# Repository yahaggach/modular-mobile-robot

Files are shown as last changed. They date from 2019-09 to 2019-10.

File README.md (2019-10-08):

# Modular Slam Robot

## Project summary

This project focuses on localization based experiments (e.g echolocation SLAM) and aims at providing a mobile modular robot. The robot and acts as a basis for various experiments with a shared mobile aspect. The modularity of the robot comes in two variants :  

  - Hardware : specific experimentation hardware can be mounted on top of the robot.
  - Software : the raspberry pi as well as power electronics ensure interoperability with most hardware.  

<p align="center">
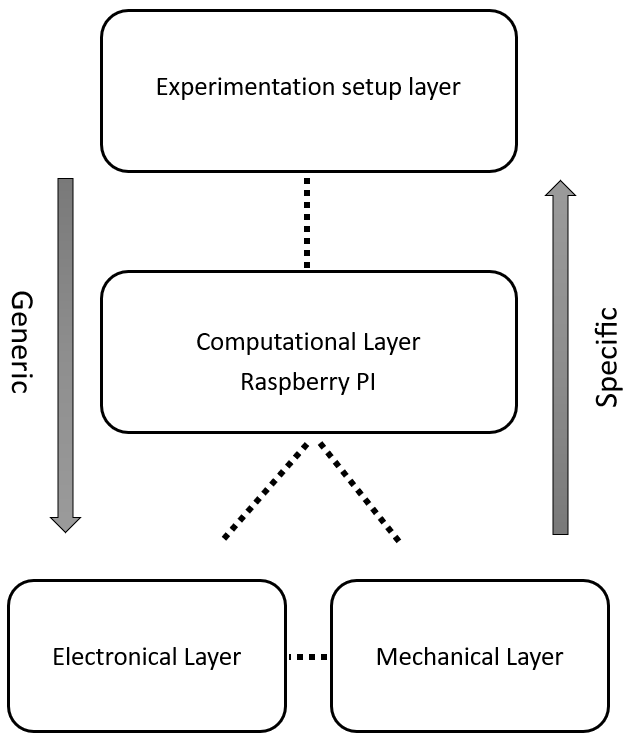
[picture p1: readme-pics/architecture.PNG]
Robot General Architecture
  
</p>  

The robot was developped at LCAV (Audiovisual Communications Laboratory) of EPFL (École Polytechnique Fédérale de Lausanne) under supervision of : Dümbgen Frederike, Krekovic Miranda and Pacholska Michalina. The robot was tested on two separate experiments : EchoSLAM and Indoor Wifi localization.  

## Robot technical summary

<p align="center">
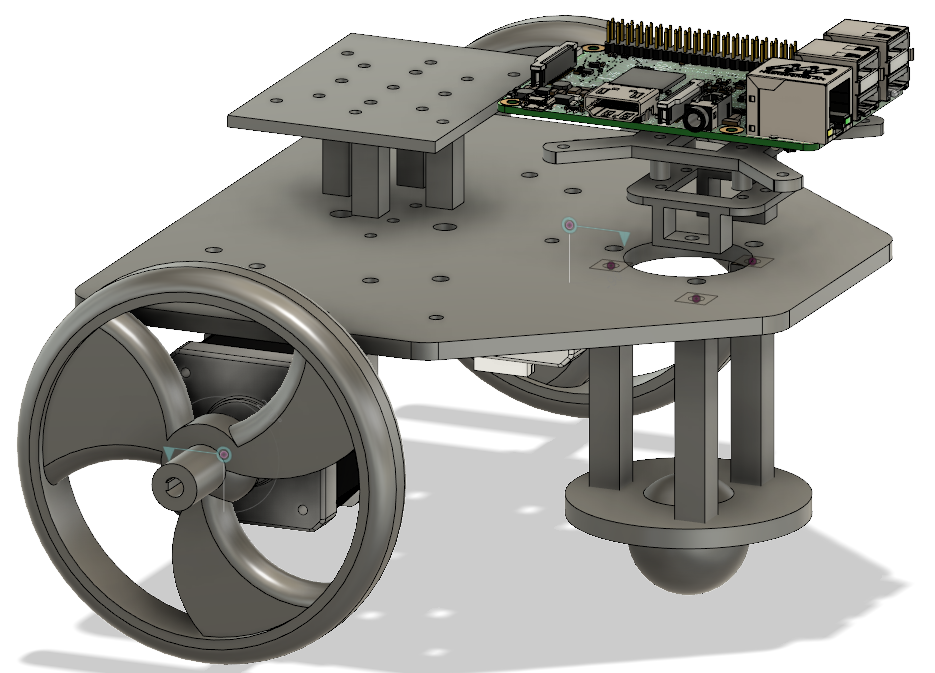
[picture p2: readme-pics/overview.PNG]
Robot Overview
  
</p>

### Mechanics

The robot's main mechanical characteristics are as follows :  

- **Differential drive** with two controlled wheels and a third free "caster ball" as support for the platform.
- **NEMA 17 stepper motors** coupled to both scooter wheels for high resolution and repeatability.
- **Laser-cut base** "parametric bolted" plate as main platform to allow mounting additional components.
- **3D printed mounts** and components for easy replacement and modification.  

All files to reproduce the robot can be found under `master/mechanical-files`. Fusion 360 files are available for modification, stl files are also available for printing with no modification. Please refer to `master/mechanical-files/drawing.pdf` for an idea about assembly. The remaining mechanical components : scooter wheels, nema 17 motors and caster ball are bought separatly and figure in the BOM `master/bill-of-materials`.  

**Any additional custom made part can still be designed, 3D-printed and assembled to the base plate using screws, nuts and one of the many holes available.**

### Electronics

A **breadboard** is used to make all the connections according to the schematics found in `master/electronic-schematics`, the breadboard then simply sticks to the base place. A **raspberry pi shield** is currently being designed and will contain all primary electronic components.  

The robot's main electronics are as follows : 

- **Raspberry pi 3 model B+** as computing unit, running the latest version of **OctoPi** (https://octoprint.org/download/).  
- **Arduino nano** running the latest version of **GRBL** (https://github.com/gnea/grbl/wiki), refer to the Frequently Asked Questions section for more details on compiling and flashing it to the Arduino Nano. Connects to the raspberry Pi using USB.  
- **TMC2208 silent stepstick** stepper drivers, connected to the arduino nano and to the stepper motors.
- **TTL Logic Level Converter** allows for communication between arduino nano and raspberry pi converts arduino's standard logic voltage of 3.3V to the raspberry pi's 5V.
- **TOF laser sensors** used to detect obstacle and measure distances.
- **18-21V rechargeable battery pack** custom made 5S2P battery pack using  10 x NCR18650 li-ion batteries with a BMS. This battery pack **can also be bought from retailers** (i.e https://voltaplex.com/5s2p-18v-6.7ah-li-ion-18650-battery-pack-panasonic-b-cuboid). Enclosure for the battery pack be designed 3D printed and mounted under the base plate between boths motors using a screw and nut. An exemple enclosure can be found under `mechanical-files/stl`, the battery pack is glued inside before assembly with base plate, a different battery pack might require a new design.
- **Step-down buck converter** to convert the voltage of the battery pack to the 5V needed to power all electronics.  

Additional electronic components may be added due to the strong interoperability of the raspberry pi. Mounts for electronic components can be designed , 3d printed and assembled by taking advantage of the many holes the plate has to offer. 

### Inverse Kinematics

The inverse kinematics of the robot are given by the following equations :  
  <br>
<p align="center">
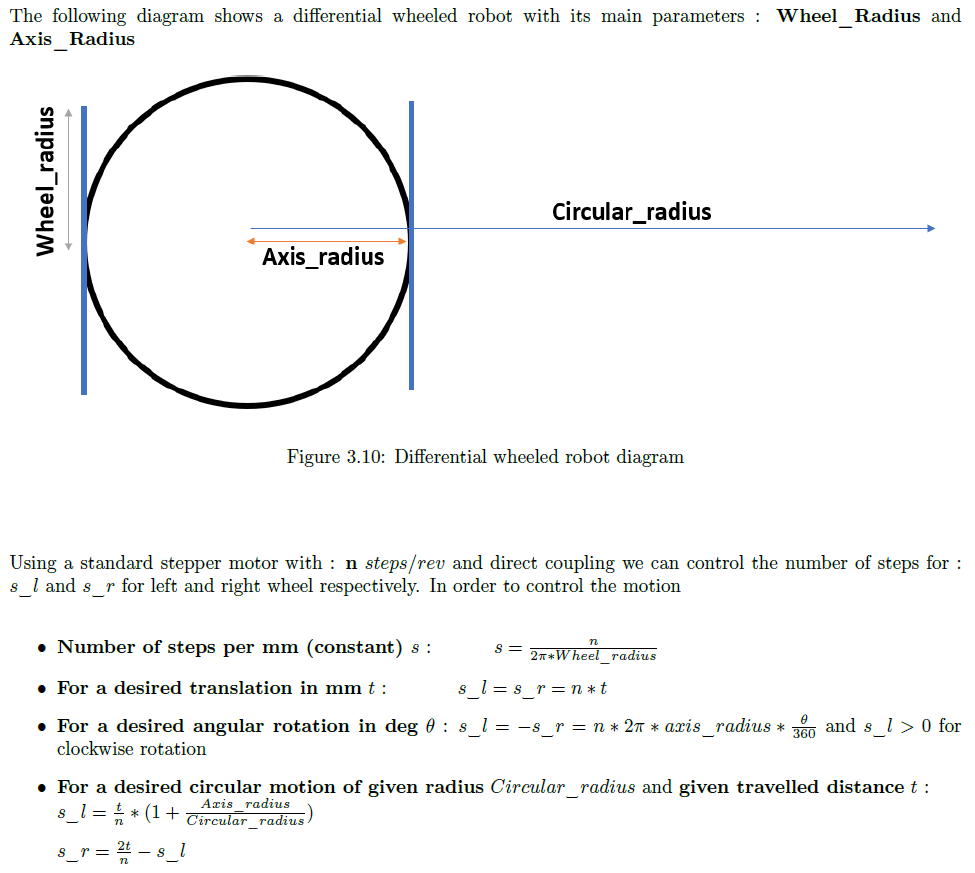
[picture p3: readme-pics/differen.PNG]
Inverse Kinematics
  
  </p>  
  
### GRBL

Grbl ( is a free and open source software that allows control of motion machines. It has a G-code interpreter and generates the proper driving signals for stepper drivers. It fits perfectly on the Arduino Nano and connects to the raspberry pi (for g-code streaming) through serial USB. The pinout of the GRBL Arduino Nano is as follows :

<p align="center">
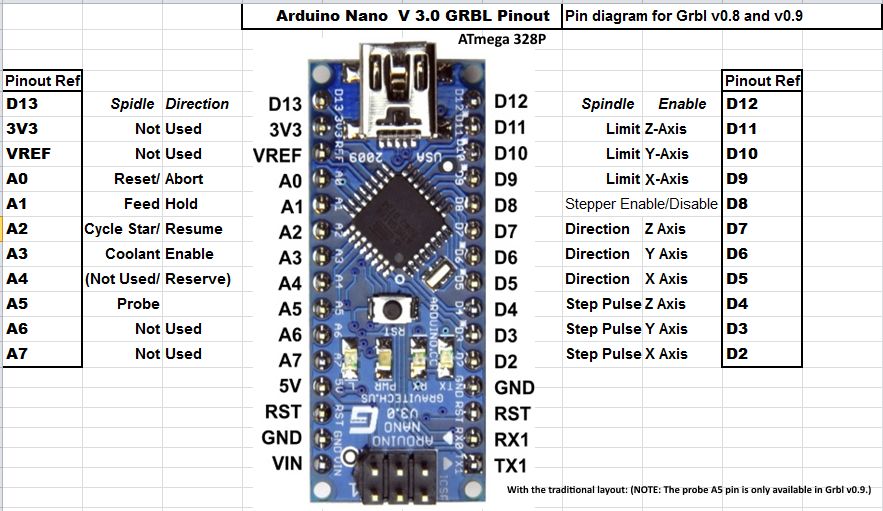
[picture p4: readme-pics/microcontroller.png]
GRBL Arduino Nano Pinout
  <br>
  <i>source : https://www.instructables.com/id/GRBL-Pinout-Arduino-Nano-v30/</i>
  </p>  
  
Pins **A0,A1,A2** can be connected to the raspberry pi's gpios (see schematics) through the TTL converter in order to stop and resume the motion through software or custom G-code command.  
GRBL needs to be configured to match with the robot's motion characteristics : **steps per mm**, **max acceleration**,**max speed...**.  
All **configuration parameters** can be found under : https://github.com/gnea/grbl/wiki/Grbl-v1.1-Configuration.  
In addition, all **supported g-code commands** can be found under : https://github.com/gnea/grbl/wiki/Grbl-v1.1-Commands.

### OctoPi

OctoPi is an OctoPrint (https://github.com/foosel/OctoPrint/wiki) image for the raspberry Pi. It is a web interface primarily intended to control 3D printers, we can however repurpose it with GRBL and consider the right wheel as the X axis and left wheel as Y axis when streaming G-code.

<p align="center">
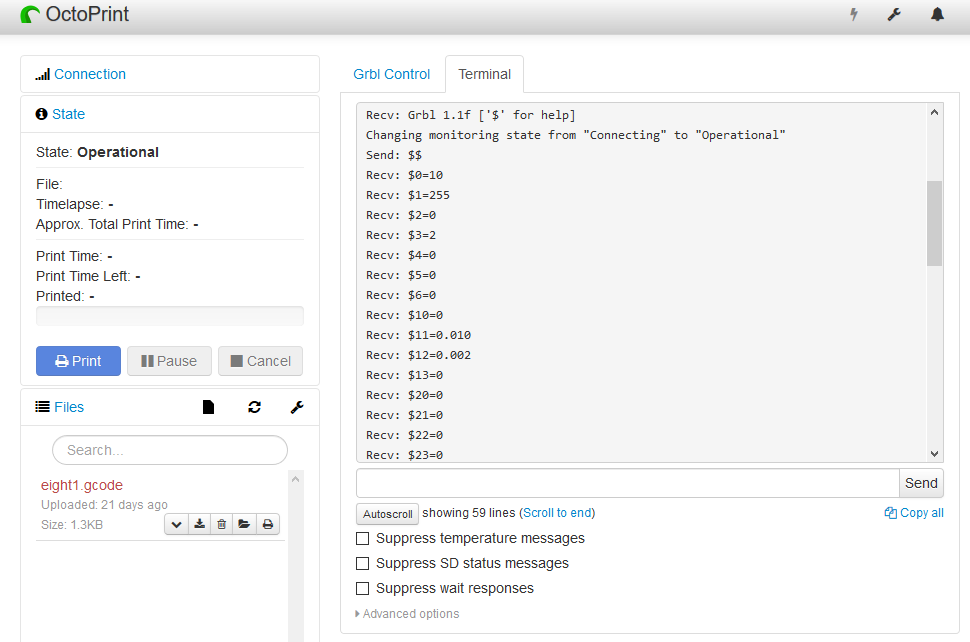
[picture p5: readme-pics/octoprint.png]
Octoprint interface
  
  </p>  
  
It is also extendable thanks to its support of user-made plugins. In order to be able to combine both GRBL and Octoprint, the following plugins must be installed through the plugin manager in Octoprint's settings :  

- **Better GRBL** (https://plugins.octoprint.org/plugins/bettergrblsupport/) allows to interface with GRBL powered microcontrollers.
- **GcodeSystemCommands** (https://plugins.octoprint.org/plugins/gcodesystemcommands/) allows to create custom G-code commands that can trigger linux or python scripts (i.e custom g-code command *OCTO 1* to turn on/off the GPIOs on the raspberry pi connected to the pins A0,A1,A2 of the Arduino Nano, see `master/electronic-schematics/ttl-raspberry.PNG` and schematics for more details)

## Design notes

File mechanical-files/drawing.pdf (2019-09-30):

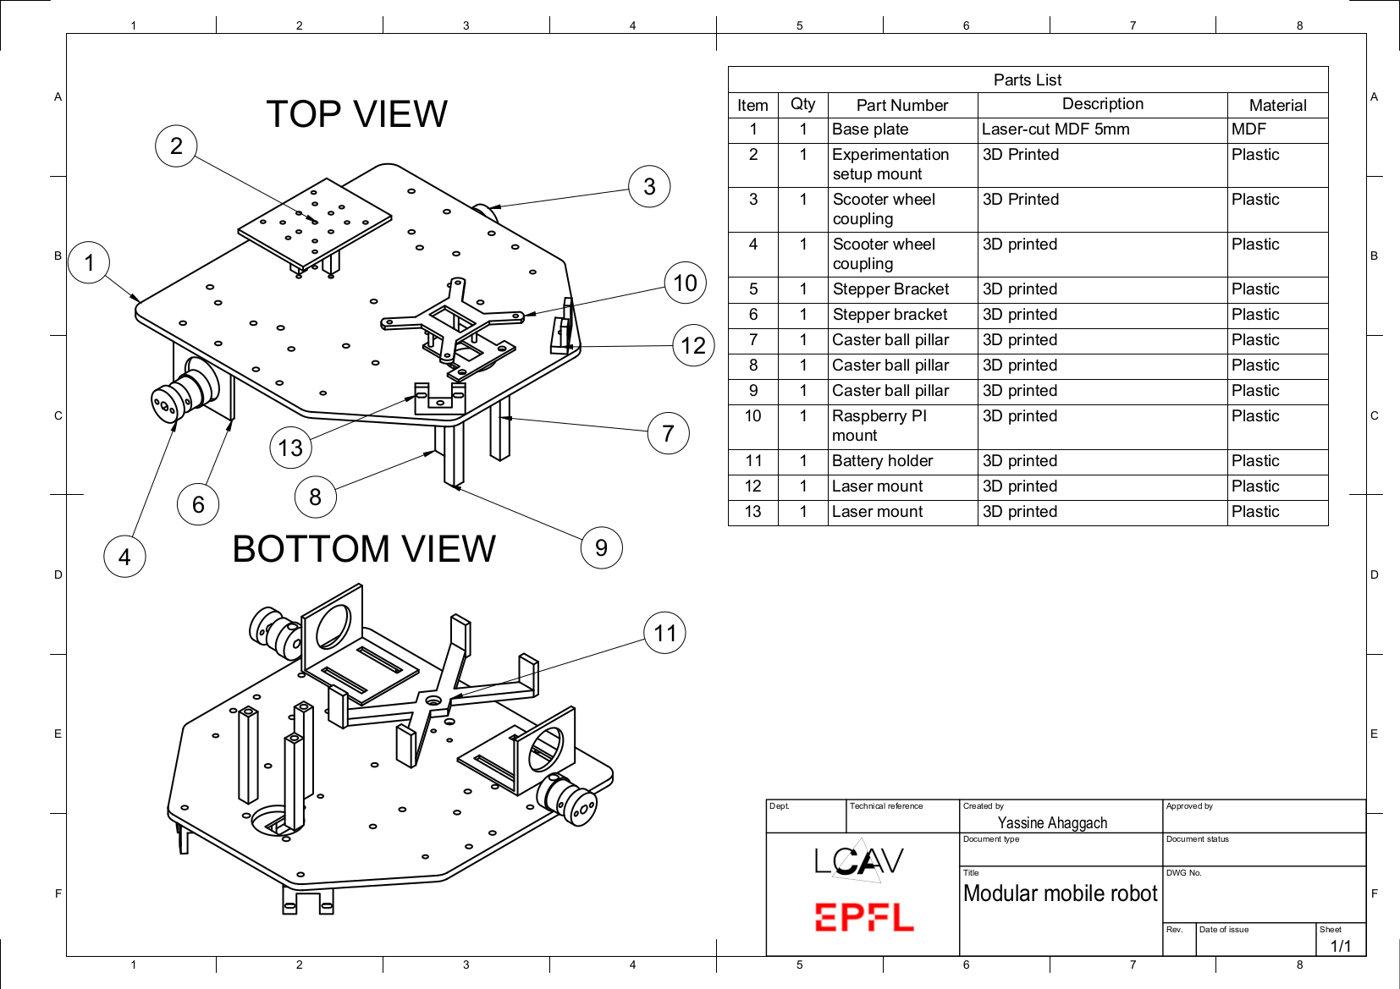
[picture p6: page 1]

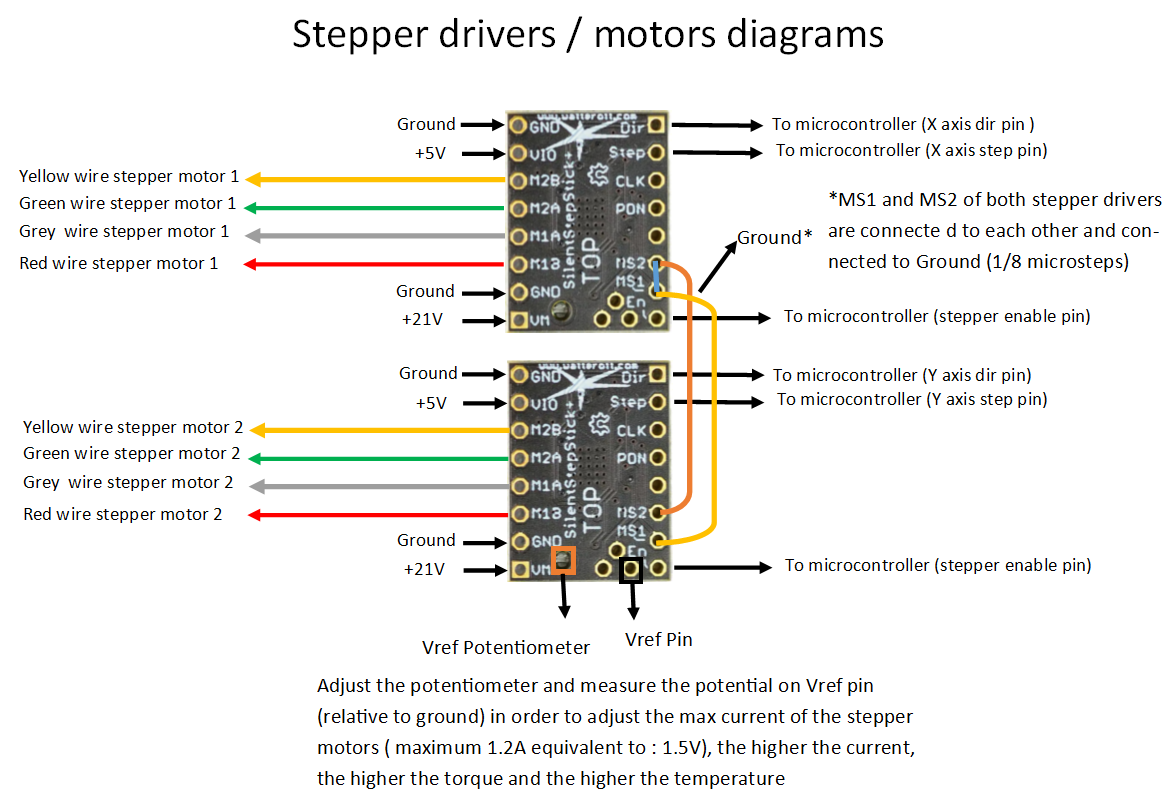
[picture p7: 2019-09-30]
electronic-schematics/stepper-schematics.PNG

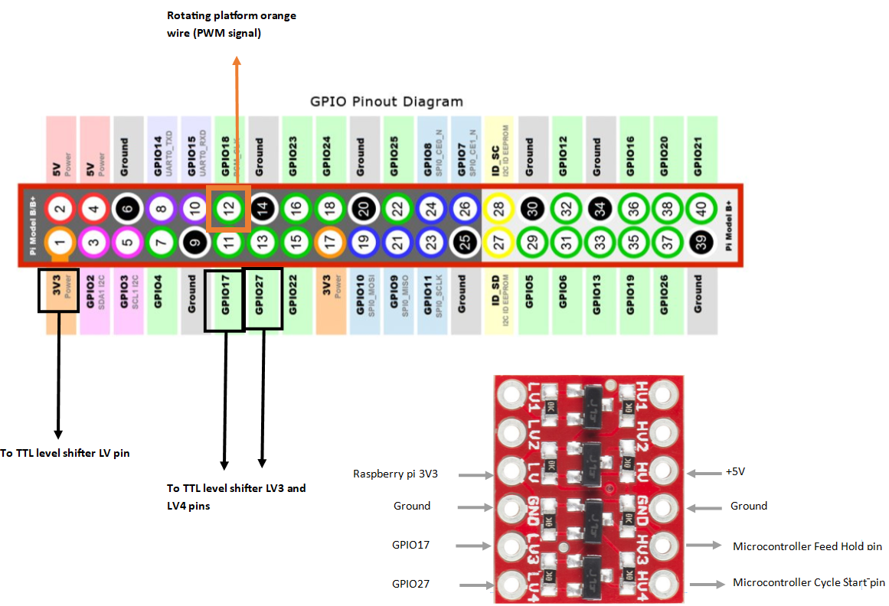
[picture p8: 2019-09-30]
electronic-schematics/ttl-raspberry-schematics.PNG

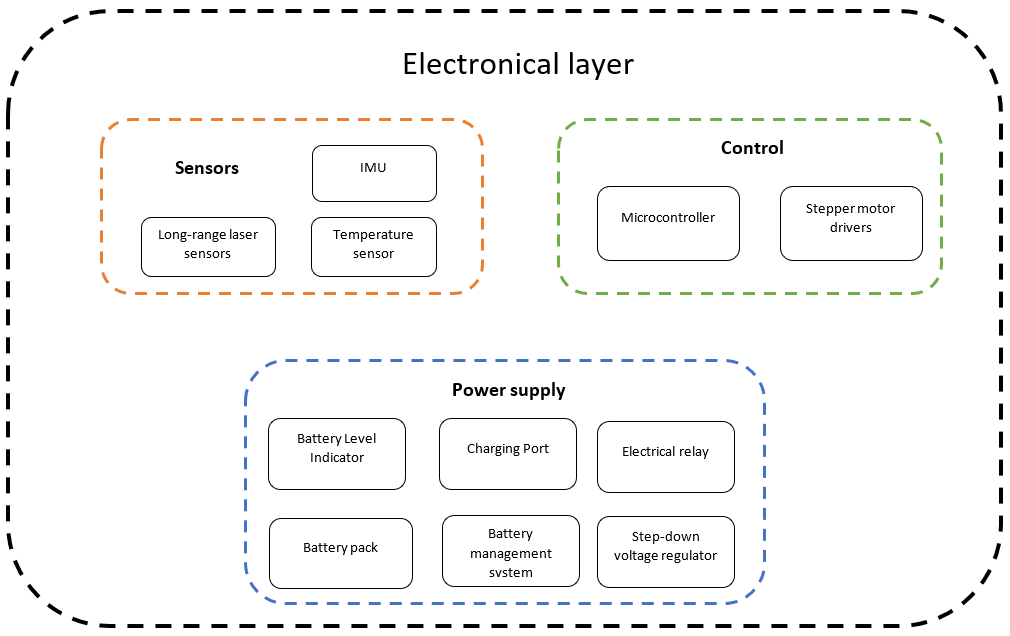
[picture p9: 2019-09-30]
readme-pics/electronical.PNG

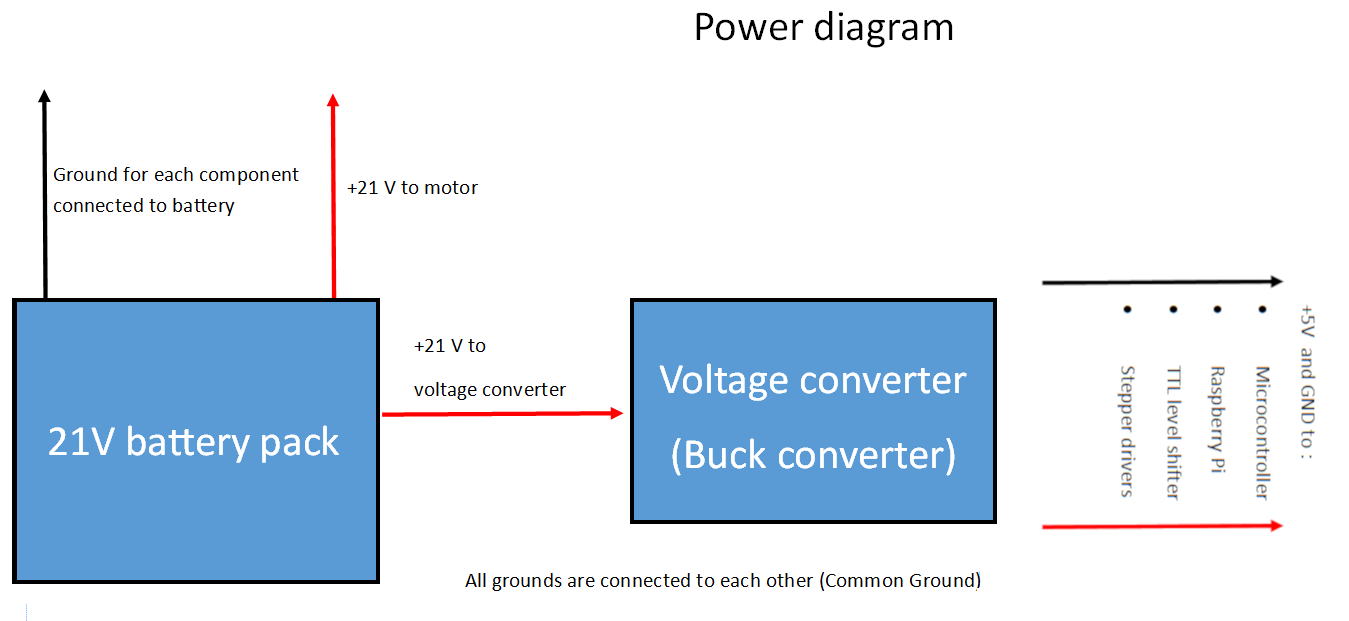
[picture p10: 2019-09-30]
electronic-schematics/power-schematics.PNG

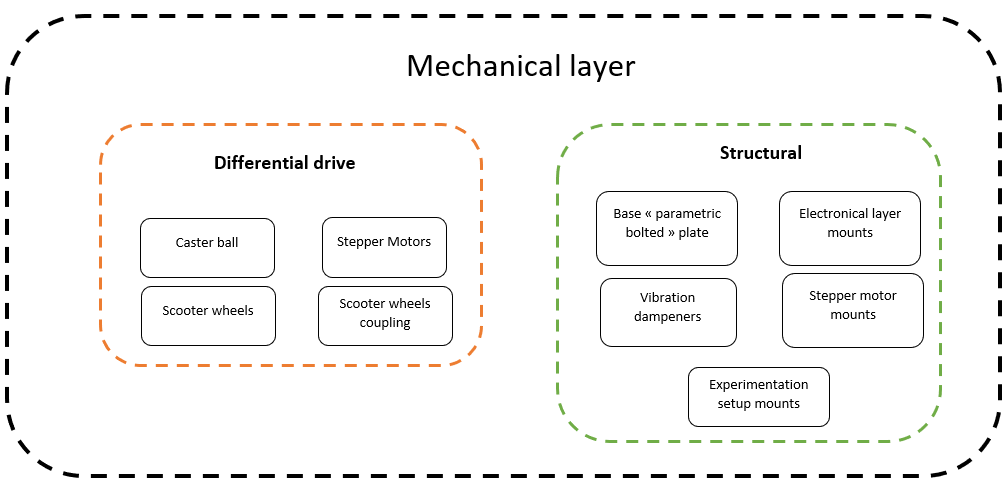
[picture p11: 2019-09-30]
readme-pics/mechanical.PNG

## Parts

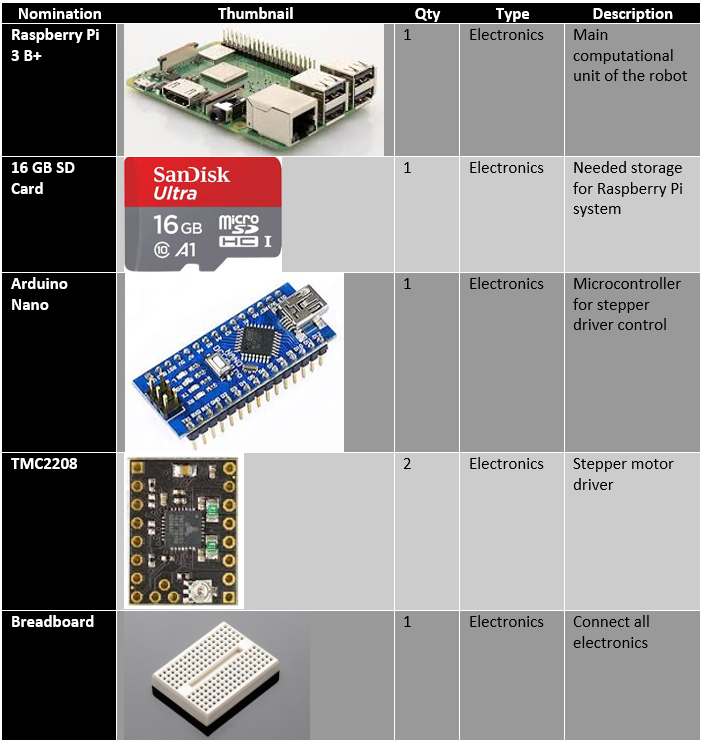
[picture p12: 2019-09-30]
bill-of-materials/BOM1.PNG

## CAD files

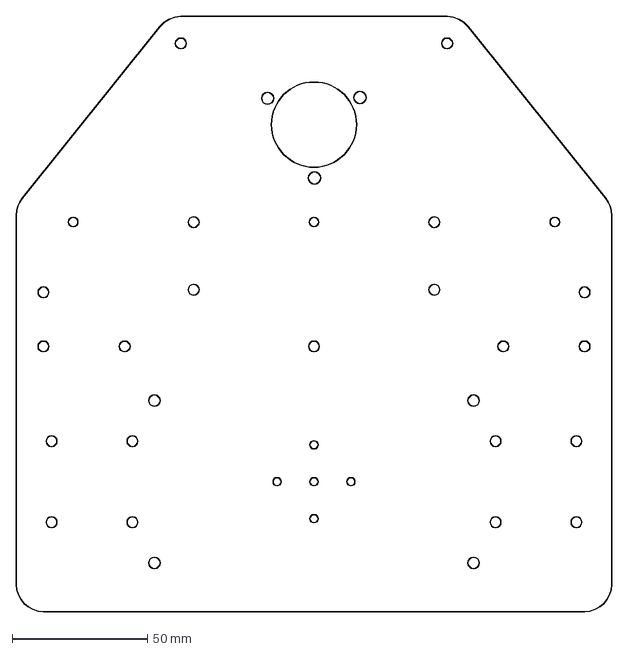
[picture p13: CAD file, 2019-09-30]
mechanical-files/Laser-cutting-base-plate.dxf
220.0 x 220.0 mm

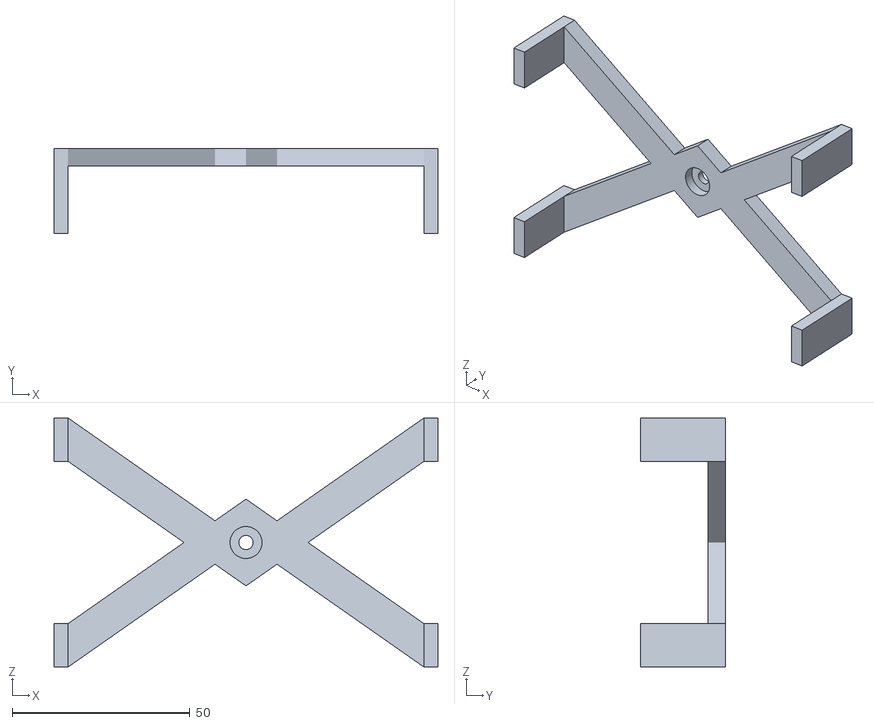
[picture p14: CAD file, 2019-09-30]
mechanical-files/stl/battery-pack.stl
108.0 x 24.0 x 70.0

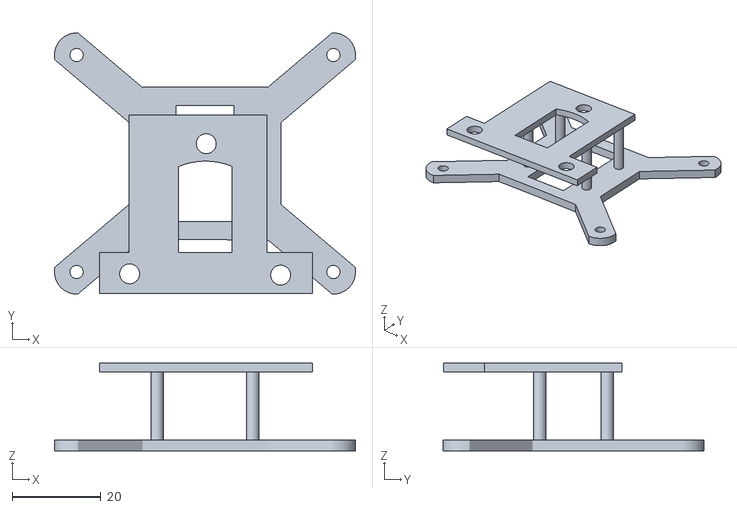
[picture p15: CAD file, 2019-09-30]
mechanical-files/stl/raspberry-pi-mount.stl
68.0 x 59.0 x 19.8

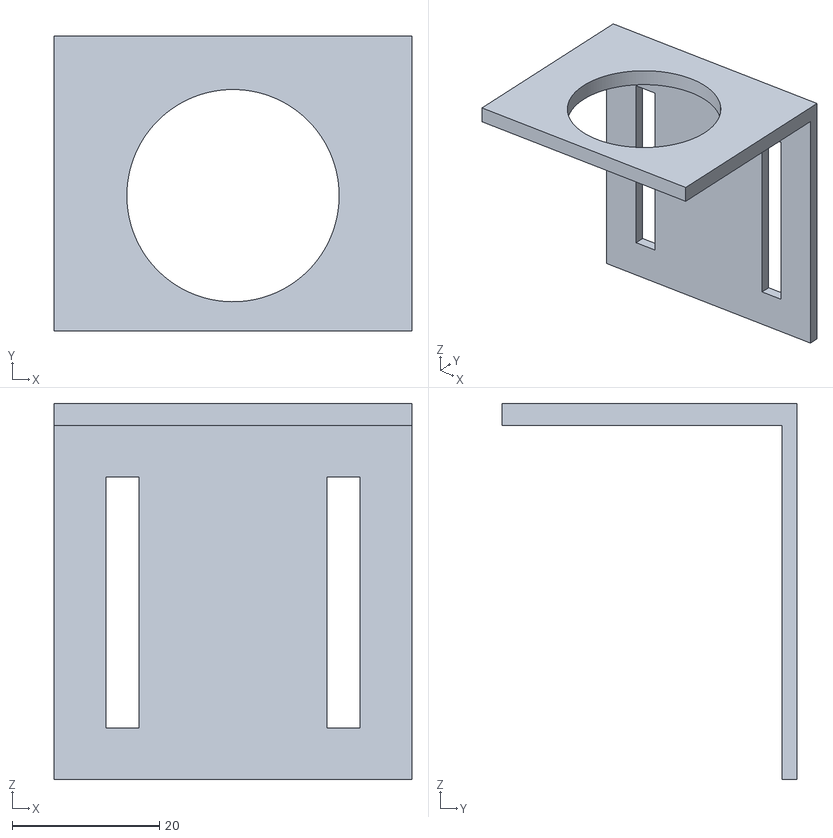
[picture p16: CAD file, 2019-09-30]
mechanical-files/stl/stepper-bracket.stl
48.5 x 40.0 x 51.0

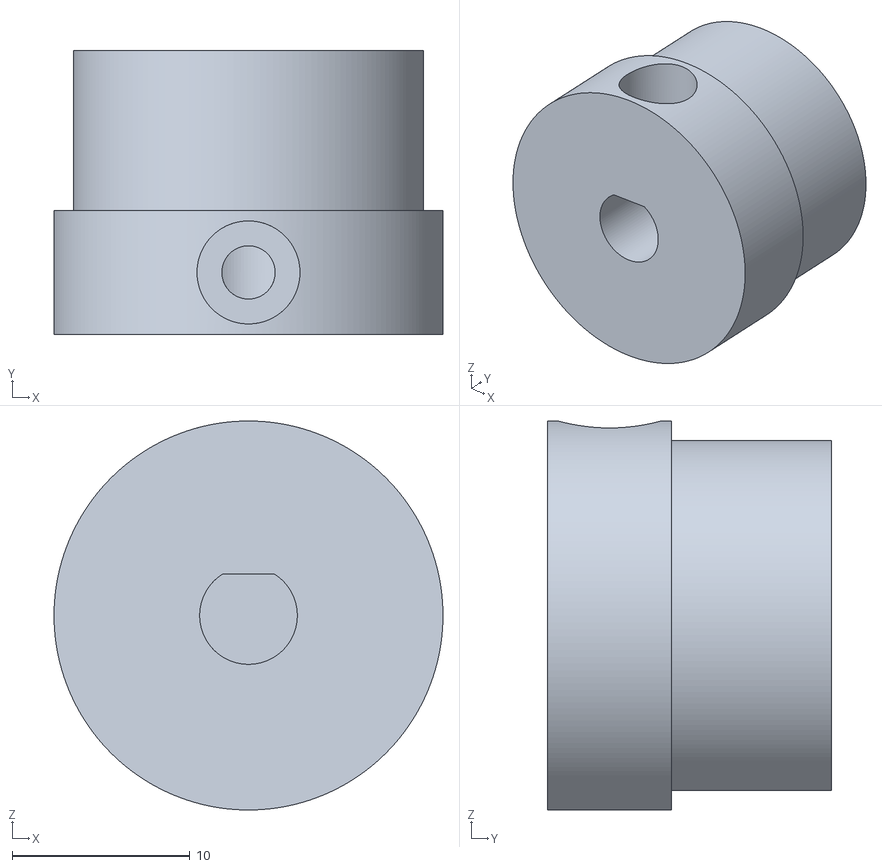
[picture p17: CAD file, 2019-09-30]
mechanical-files/stl/wheel-coupling-1.stl
21.9 x 16.0 x 21.9

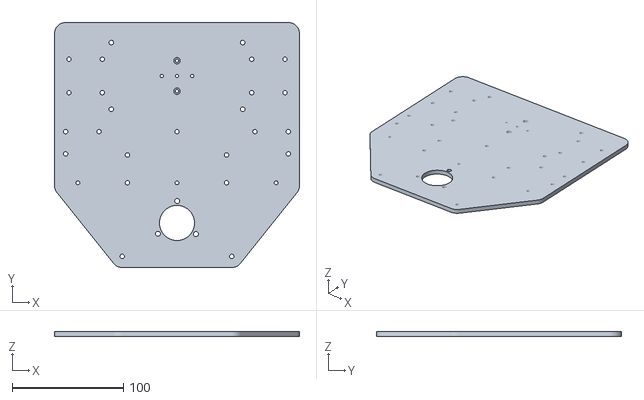
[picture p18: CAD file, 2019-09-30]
mechanical-files/stl/base-plate.stl
220.0 x 220.0 x 4.50

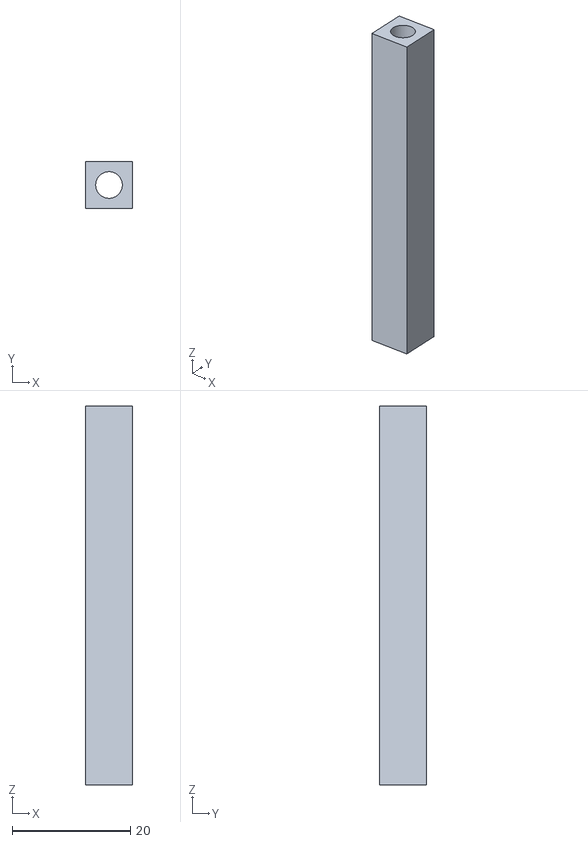
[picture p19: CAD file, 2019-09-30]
mechanical-files/stl/caster-ball-pillar.stl
8.00 x 8.00 x 64.0

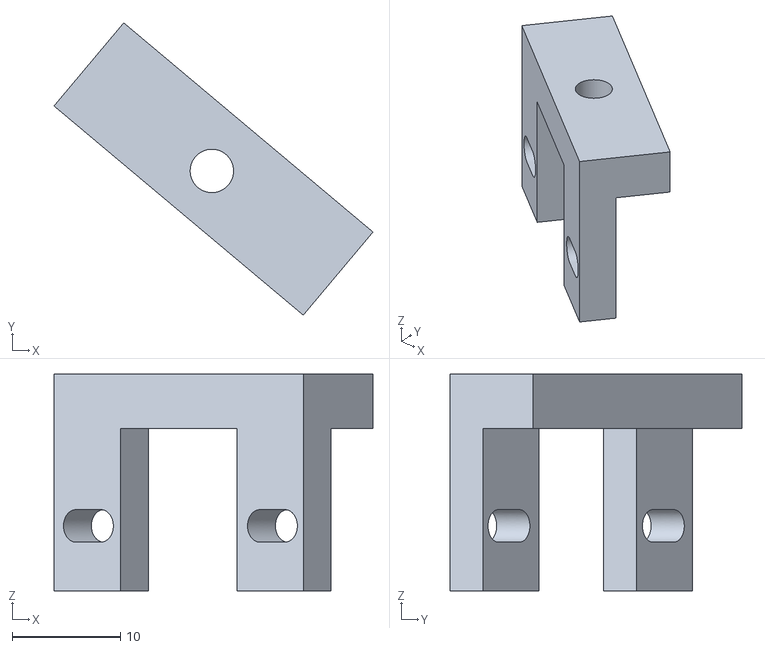
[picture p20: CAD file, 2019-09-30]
mechanical-files/stl/laser-mount.stl
29.4 x 26.9 x 20.0

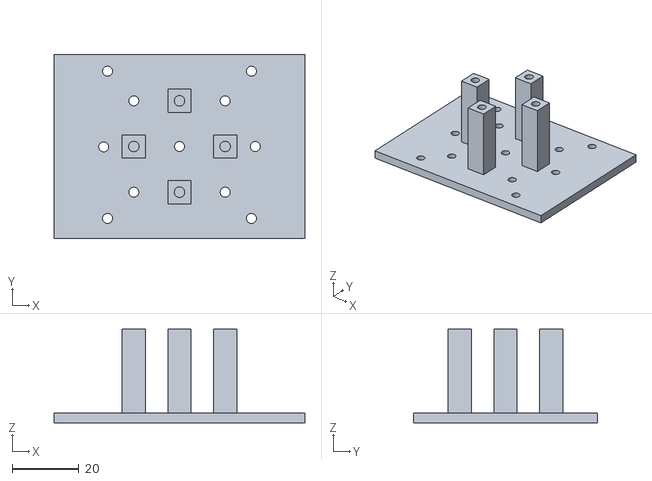
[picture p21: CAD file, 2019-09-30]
mechanical-files/stl/experimentation-setup-mount.stl
75.0 x 55.0 x 28.0

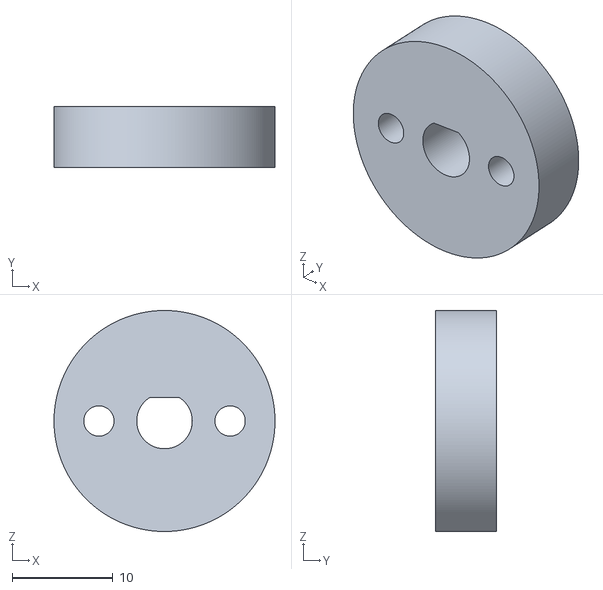
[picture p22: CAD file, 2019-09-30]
mechanical-files/stl/wheel-coupling-2.stl
21.9 x 6.00 x 21.9

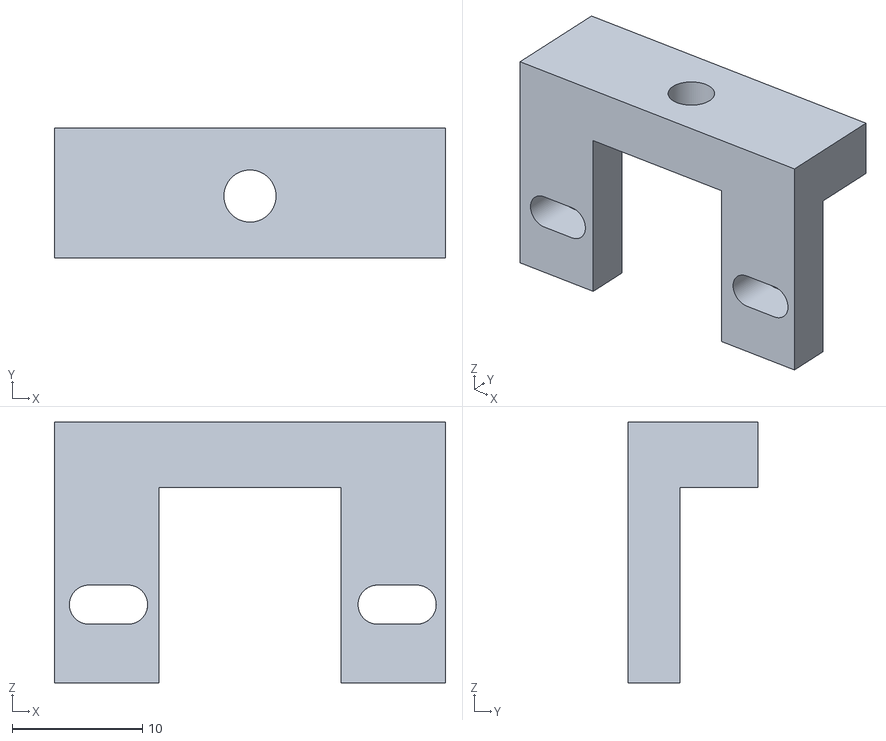
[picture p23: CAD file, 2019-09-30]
mechanical-files/stl/laser-sensor-mount.stl
30.0 x 10.0 x 20.0

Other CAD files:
mechanical-files/modular-robot.f3d

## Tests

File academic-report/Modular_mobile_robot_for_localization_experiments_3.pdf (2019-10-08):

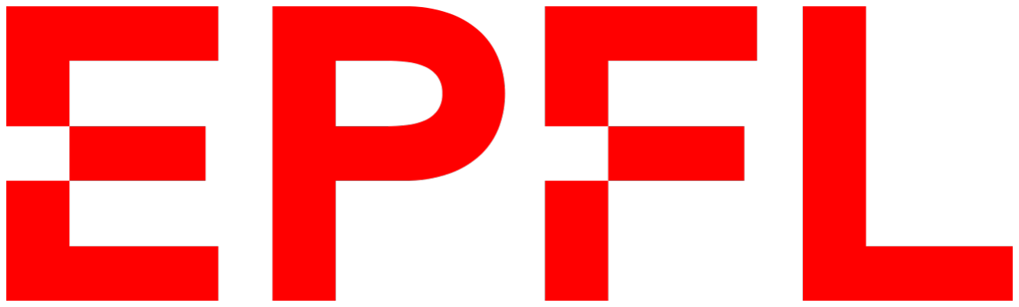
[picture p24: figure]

# Modular mobile robot for localization experiments

Semester Project

Author :

Ahaggach Yassine

Supervisors :

Frederike Dümbgen
Miranda Kreković
Michalina Pacholska
Mihailo Kolundžija

October 8, 2019

MT-RO MA2

# Contents

1 Introduction | 3
2 List of specifications | 4
3 Robot presentation | 5
4 Accuracy and precision evaluation | 12
5 Conclusion | 15
6 Annex | 16

7 Bibliography | 25

# 1 | Introduction

Academic research is a complex field combining both theory and practice. From elaborating leads and hypotheses to thorough practical experimentation, research is a cyclic process where several attempts are expected before achieving any concrete result. In order to be as efficient as possible, balancing between both practice and theory in terms of material and time resources is of critical importance.
Experimentation usually amounts to data gathering (measurements), processing and evaluation (ground truth comparison). However, due to the uniqueness of each different research subject as well as imposed performance constraints, the setup and protocol can vastly differ.
In light of this context, automation in regards to conducting experiments contributes largely to streamlining and speeding up the research process. Empowering researchers with experimentation platforms grants them the freedom to manage their time and efforts as they see fit and provides them with characterized proven tools to support their work.
This project focuses on localization based experiments (e.g echolocation algorithms) and aims at providing a mobile modular robot. The robot acts as a basis for various experiments with a shared mobile aspect. The idea behind this project stems from the following observations :
- An autonomous modular mobile robot is a solution to the previously outlined challenges regarding research.
- The current state of mobile robots shows few to none, scalable modular mobile robots capable of interfacing with the various setups needed.
- Custom solutions are the expensive but conventional way to go to automate mobile experiments.
- It is often a matter of one or two components that differentiate one mobile experimentation setup from the other .

Currently supporting two experiments (echoSLAM and indoor wifi based localization), the robot’s core design in hardware and software revolves around ease of use and modularity. The robot is precise, easily controllable and allows to effortlessly retrieve experimentation data.
With affordable and available materials, anyone with the plans as well as the documentation is capable of easily reproducing and repurposing the robot.

# 2 | List of specifications

The robot is an autonomous modular mobile platform that run various experiments. Each experimentation setup shares and connects to the same mobile platform and is supported by the structure.Through analysis of the robot’s main tasks, the specifications to respect are as follows :

1. Scalability : The robot’s design is scalable. In terms of mechanical and electronical performance, adding a complex experimentation layer should cause no issue.
2. Reproducibility : The robot’s specific mechanical parts are easily reproducible through simple popular manufacturing processes (3d printing, laser cutting ...).
3. Mechanical modularity : The robot’s design allows for additional mechanical parts to be assembled as to support specific experimentation setups.
4. Load : The robot must bear the additional load of the various experimentation setups with no impact on the performance.
5. Exteroception : The robot is capable of obstacle avoidance.
6. Resolution of motion : The robot is intended to operate in regular sized rooms (7-8m width) , the resolution is nominally set to be ≤ 1 [cm].
7. Precision of motion : The control of the robot is repeatable, the motion characterization is well defined.
8. Trajectory following : The robot is capable of smooth and precise trajectory following.
9. Interfacing (electronics/software modularity) : The robot supports most communication protocols and is capable of interfacing with a wide range of components.
10. Data gathering : The robot logs all data general and specific to the experiments and provides the user with a compiled archive at the end of each experiment run.
11. Communication : The robot’s architecture allows for it to easily integrate other systems (camera tracking systems ,database...)
12. Autonomy : The robot runs on rechargeable batteries that can hold for several runs of the experiment. The battery also powers the experimentation setup.
13. Ergonomy : The robot is user friendly. Running experiments on the robot is automated and needs minimal to no intervention.

# 3 | Robot presentation

## 3.1 General Overview

The robot’s architecture is based on a layers concept. Lower layers are for electronical / mechanical functions : power supply, control and localization of the robot (generic tasks that are shared among different experiments) while outer layers are specific to the experiment (e.g microphone + speaker for echo based experiments).


Figure 3.1: Global architecture

Each layer is designed independently with the specifications in mind. The idea is to achieve the most scalable, inter-operable system. Each layer can be replaced, modified and upgraded independently and still maintain normal functioning of the robot.

### 3.1.1 Electronical layer

The following diagram shows the electronical layer in detail :


Figure 3.2: Electronical layer

The electronical layer is comprised of three main modules :

- Power supply : this module is in charge of providing power to the whole system. The solution is based on a rechargeable battery pack with battery management system and level indicator. Components from the outer layer are either low consumption components (typ. 5V) which are powered through the step down voltage regulator, or high consumption components (typ. 12V) which are directly powered from the battery pack and turned on or off through the electrical relay. This configuration allows for stable and efficient operation power wise.
- Sensors : this module provides the general data of the mobile robot. Long-range sensors are used for distance and proximity sensing. The IMU is constituted of a gyroscope, an accelerometer and a magnetometer. The temperature sensor gives ambient temperature readings. These information are not necessarily relevant to the experiment but could provide insight if needed on the external conditions.
- Control : In order to control the stepper motors, drivers are needed. The drivers are circuitry capable of commanding stepper motors. The drivers are in turn controlled through a microcontroller.

### 3.1.2 Mechanical layer

The mechanical layer is made of two main modules :


Figure 3.3: Mechanical layer

- Differential drive : The robot is a differential wheeled robot. Two scooter wheels coupled to stepper motors drive the robot. A caster ball is used as free rolling ball to provide stability to the system and offload the motors.
- Structural module : The mechanical modularity of the robot is represented through the base "parametric bolted" plate which is basically a plate with a fixed number of holes distributed in a parametric way. The holes allow to assemble to the plate various mounts ( e.g raspberry pi mount, stepper motor mounts) connecting thus "mechanically" the various components of the robot. Vibration dampeners are also used to reduce stepper motor vibrations.

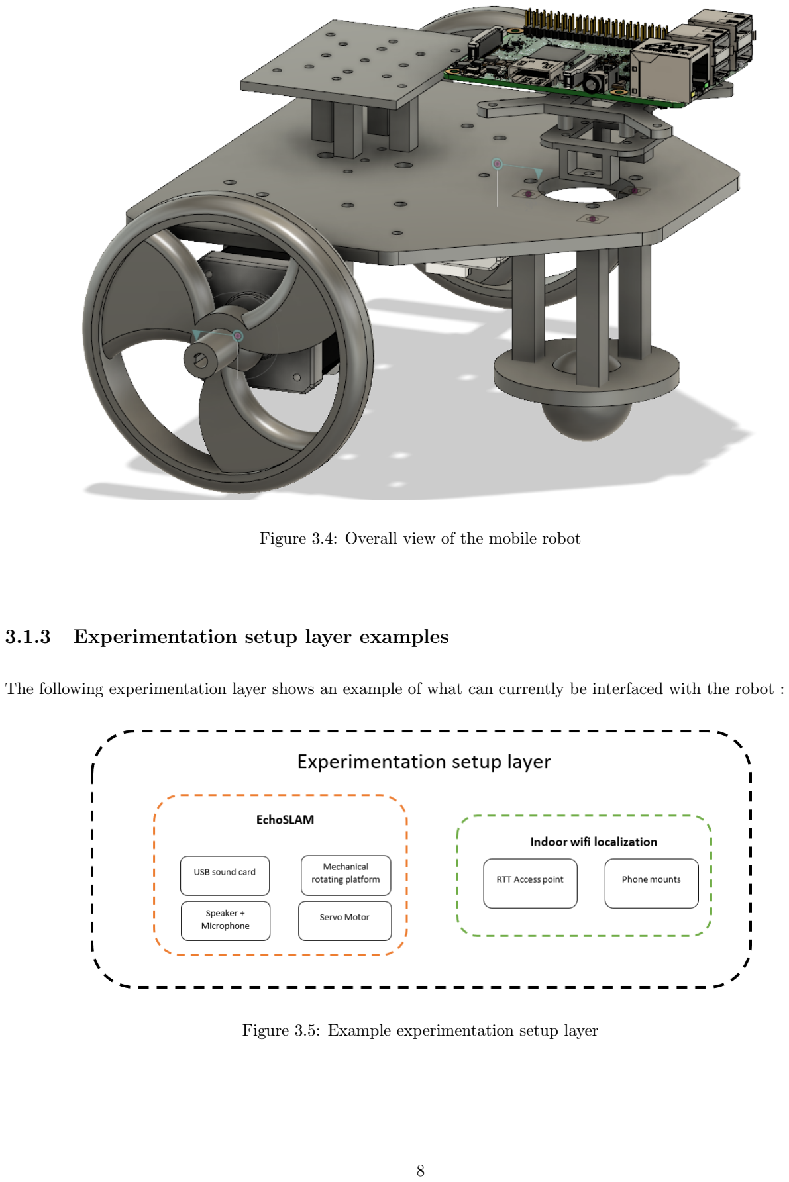
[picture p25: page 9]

Figure 3.4: Overall view of the mobile robot

### 3.1.3 Experimentation setup layer examples

The following experimentation layer shows an example of what can currently be interfaced with the robot :

Figure 3.5: Example experimentation setup layer

## 3.2 Critical choices and justification

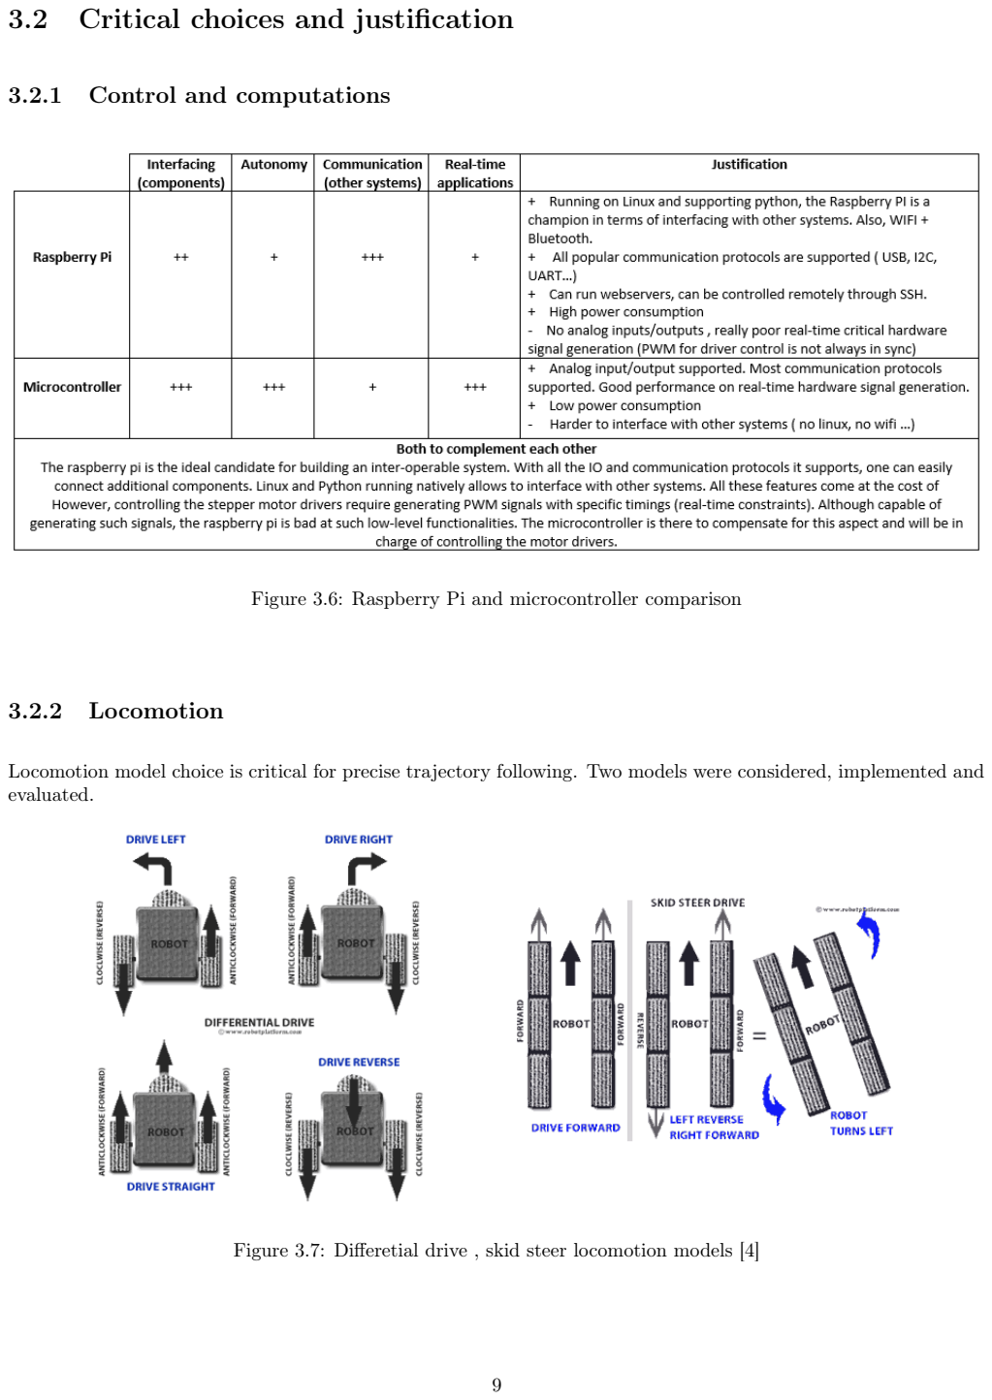
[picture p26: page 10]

### 3.2.1 Control and computations

Figure 3.6: Raspberry Pi and microcontroller comparison

### 3.2.2 Locomotion

Locomotion model choice is critical for precise trajectory following. Two models were considered, implemented and evaluated.

Figure 3.7: Differetial drive , skid steer locomotion models [4]

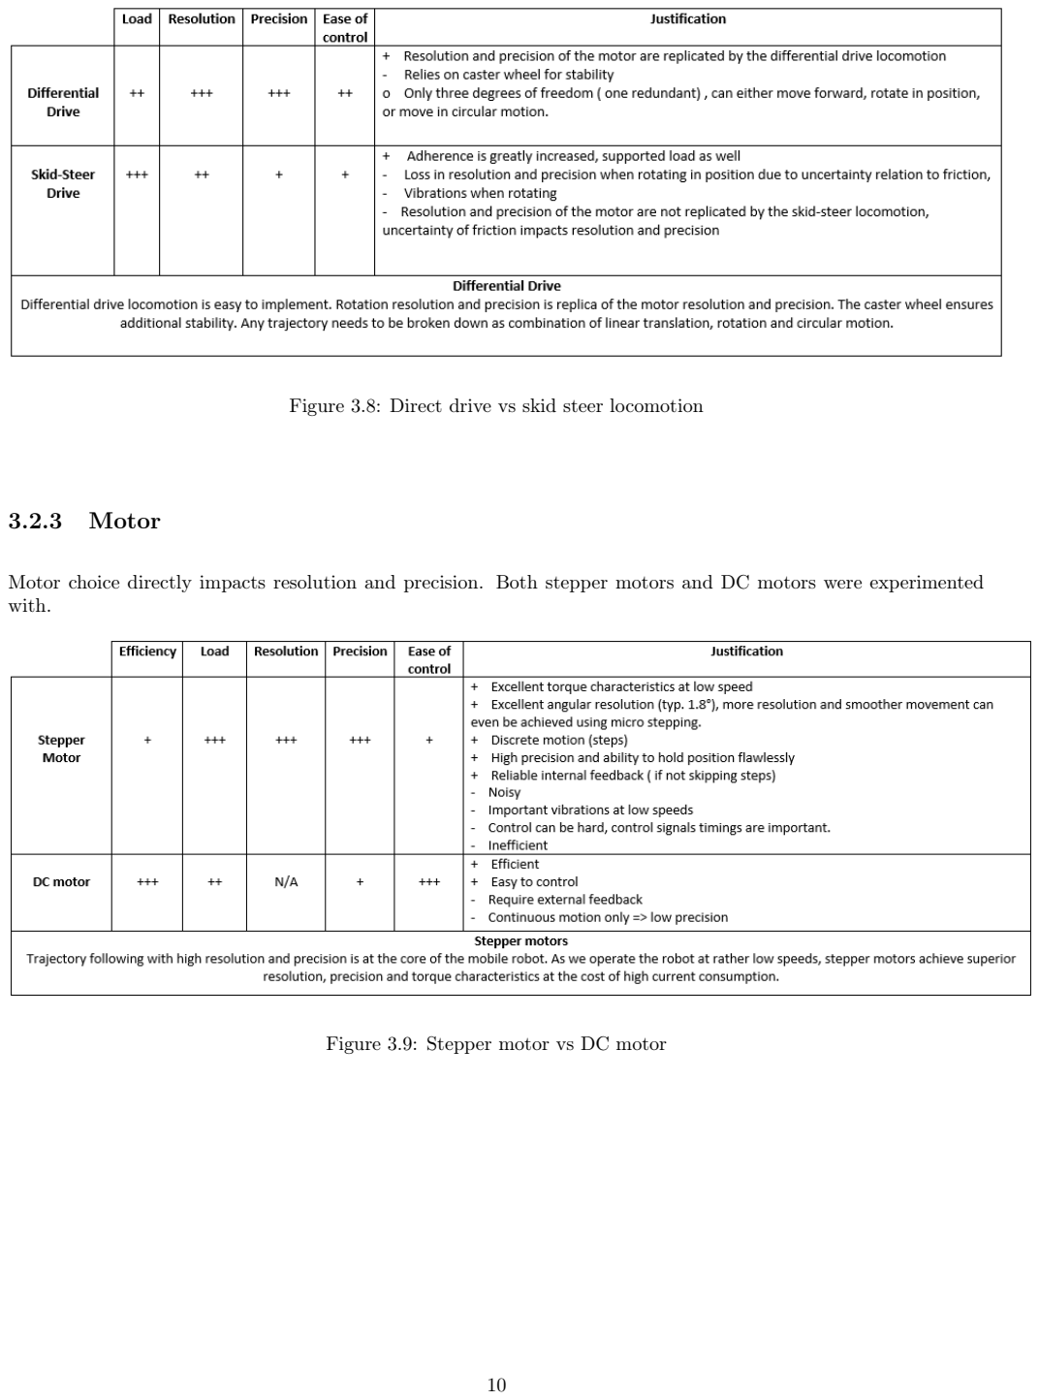
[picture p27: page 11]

Figure 3.8: Direct drive vs skid steer locomotion

### 3.2.3 Motor

Motor choice directly impacts resolution and precision. Both stepper motors and DC motors were experimented with.

Figure 3.9: Stepper motor vs DC motor

## 3.3 Differential drive motion inverse kinematics

The following diagram shows a differential wheeled robot with its main parameters : Wheel_Radius and Axis_Radius

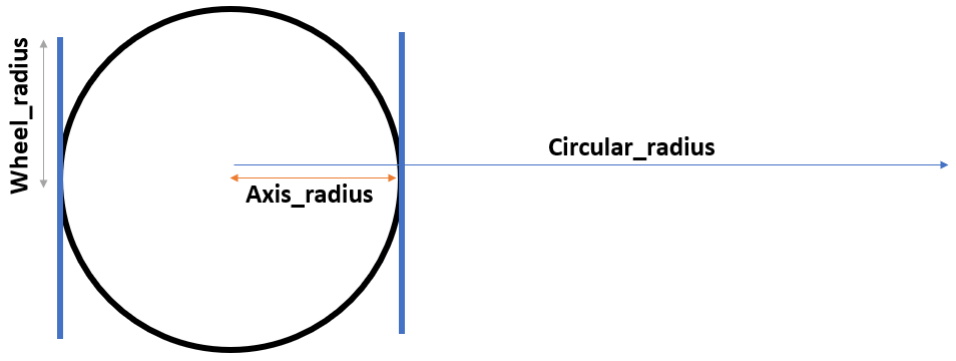
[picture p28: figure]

Figure 3.10: Differential wheeled robot diagram

Using a standard stepper motor with : n steps/rev and direct coupling we can control the number of steps for : s_l and s_r for left and right wheel respectively. In order to control the motion

- Number of steps per mm (constant) s : | s =

n
2π∗W heel_radius
- For a desired translation in mm t : | s_l = s_r = n ∗ t
- For a desired angular rotation in deg θ : s_l = −s_r = n ∗ 2π ∗ axis_radius ∗

θ
360 and s_l > 0 for
clockwise rotation
- For a desired circular motion of given radius Circular_radius and given travelled distance t : s_l =

t
n

∗ (1 + Axis_radius
Circular_radius )

s_r =

2t
n − s_l

# 4 | Accuracy and precision evaluation

## 4.1 Accuracy and precision of stepper motors

The choice of stepper motors benefits both resolution and accuracy. The working principle behind stepper motors is illustrated in the following figure

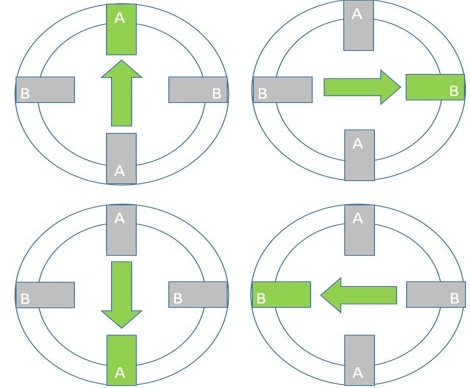
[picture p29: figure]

Figure 4.1: Stepper Motor 1-Phase on full rotation [1]

By energizing a coil ( or couple of coils ), a magnetic field of known direction is generated. The rotor ( green arrow in the picture ) aligns itself with the generated magnetic field. And thus in discrete steps, we can rotate the rotor by continuously energizing the following coil in sequence. A position can be held accurately by stopping the sequence at any given time and keeping the corresponding coil energized. The currently used stepper motor is a NEMA17 with 200 steps per revolution (corresp. 1.8° resolution). Therefore, in theory, inaccuracy is only due to the discrete nature of movement.
In order to increase the resolution and achieve smoother movement, microstepping is used. Microstepping is illustrated in the following figure :

Figure 4.2: Symbolic example of quarter-stepping in a bipolar stepper motor [3]

The resolution is limited by the number of steps per revolution the motor has which is defined in turn by the number of discrete magnetic field directions the rotor is able to align itself with. By energizing several coils with different voltages at the same time we are able to create additional intermediate stable magnetic field directions thus increasing the resolution. This comes at the cost of effective torque which decreases as the intermediate magnetic field will never be as strong at the natural one (aligned with coil). If the power to the steppers is cut, additional inaccuracy can be introduced because of microstepping. The robot is more prone to loose the position of the rotor in these weaker intermediate steps.

## 4.2 Systematic evaluations

In order to assess the accuracy and precision of the robot, the various type of motions are evaluated. The observed motion under several runs of translation, rotation and circular motion is compared to the given command. Since we are using a 1/16 microstepping factor, a stepper with 200 steps/rev (1.8° per step) and a scooter wheel of nominal diameter 100 mm we have a resolution ∆d = π ∗ 100 ∗

1.8
360 ∗

1
16 = 0.1[mm].As such, and due to the stepper motor technology, accuracy and precision are not expected to change over different distances travelled by the robot.

### 4.2.1 Translation motion

To evaluate translation, the robot is tasked to move forward by 500 mm and backwards by 500 mm for 20 runs, the results are as follows :

F orward 500mm
50.2 | 50.5 | 50.4 | 51 | 50.2
50.3 | 50.1 | 50.5 | 50.4 | 50.1
50.4 | 50.6 | 50.5 | 50.2 | 50.2
50 | 50 | 50.1 | 50 | 50.2
Mean | 50.295
ST D | 0.248

Backward 500mm
| 50.1 | 50.5 | 50 | 50 | 51
| 50.4 | 50.4 | 50.4 | 50.4 | 50
| 50 | 50.4 | 50.2 | 50.4 | 50.2
| 51 | 50 | 50.4 | 50.1 | 50.2
Mean | 50.305
ST D | 0.294

Figure 4.3: Evaluation of robot’s performance for linear translation

We can observe really low STD and good average. The system is precise and accurate for linear translations. The obtained error could stem from the measuring technique. The evaluation of translation is critical as it is directly linked to the distance travelled by each wheel. The differential drive locomotion model has free rotation (no skid) therefore the distance travelled by each wheel is deterministic for good characterization of angle and rotation center .

### 4.2.2 Rotation and circular motion

Several runs have been made for rotation and circular motion of radius R. These runs have shown impeccable precision for angular rotation (given correct calibartion). Rotation center shifting has proven itself hard to evaluate due to the fact that the shift is so little < 1[mm] that any actual measurement would rather show inaccuracy in measurement technique over inaccuracy of motion.

# 5 | Conclusion

Globally, the project has been really challenging, requiring several iterations before reaching satisfying results. The robot stayed true to its original purpose : a modular DIY mobile platform for running experiments. Some key points justifying the robot meeting the specifications set :

- By running 3d printing firmware and using a microcontroller to control the stepper drivers, synchronization between both wheels is ensured.
- The robot benefits largely from the precision and accuracy stepper motors have to offer.
- The several holes on the mounting plate are more than enough to assemble any additional mounts and components.
- The raspberry pi hosts a user friendly interface for easy control and configuration of the robot.

Some points could however still be improved :

- The robot could benefit from higher grade and capacity batteries than the current 18650 li-ion ones.
- The scooter wheels start to show some wear, potentially leading to loss in resolution and accuracy.
- The caster ball shows wear as well, need for cleaning and lubricating to ensure optimal functioning.
- The differential drive locomotion model is not holonomic and constrains the user to break down parametric trajectories to linear translations, in position rotations and radius based turns.

# 6 | Annex

## 6.1 Bill of Materials

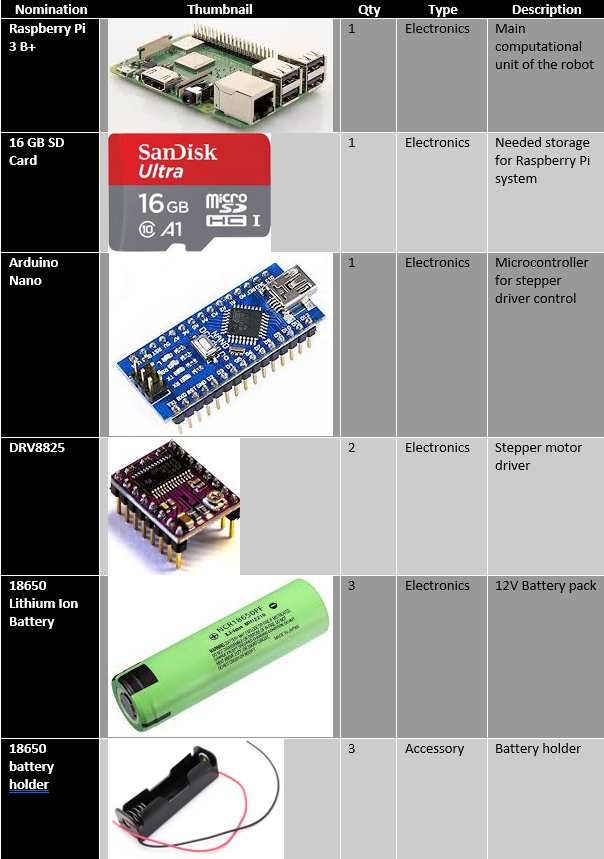
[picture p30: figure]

Figure 6.1: BOM 1/3

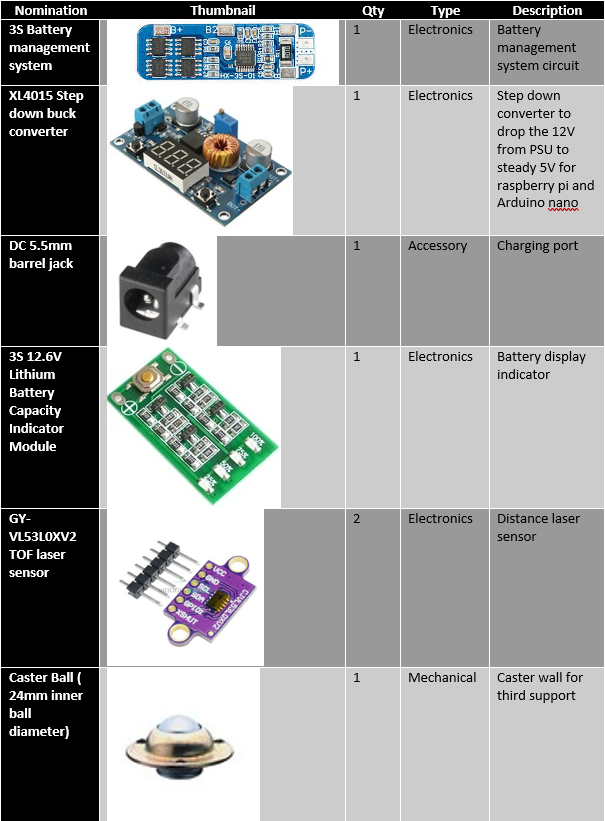
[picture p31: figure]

Figure 6.2: BOM 2/3

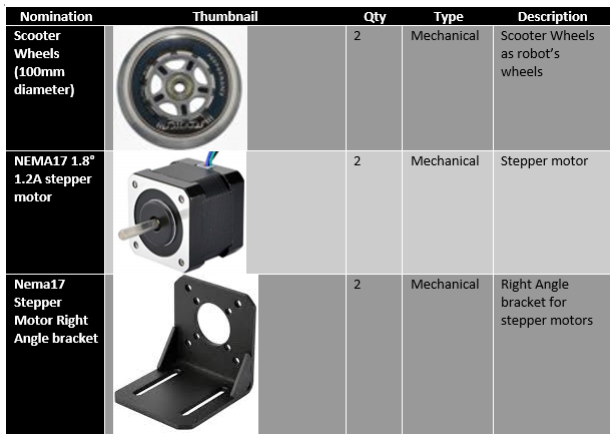
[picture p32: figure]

Figure 6.3: BOM 3/3

## 6.2 Designs and Assembly

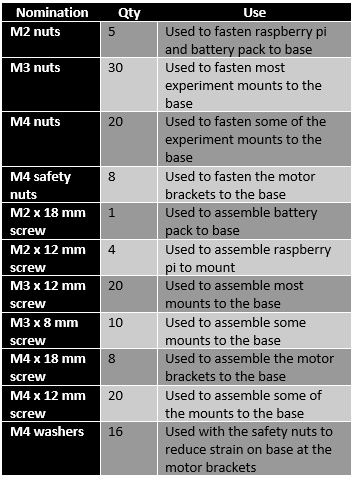
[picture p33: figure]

Figure 6.4: List of needed screws and nuts


Modular mobile Robot

## 6.3 Software

The raspberry pi automatically connects to any wifi with the following characteristics :
SSID : Robot
Password : Robot0101
The user needs to make sure before turning on the robot that such wifi exists, mobile hotspots work as well. Once connected, and the local IP address of the rasberry pi fetched, the user can SSH with the following credentials : Username : pi
Password : raspberry
A zip file containing all material relative to an experiment (EchoSlam) is generated at the /home/ folder of the raspberry pi. To access it and download it, use FileZilla and initiate a connection as follows :
IP : *RaspberryPILocalAddress*
Port : 22
In case of using a soundcard, the volumes can be adjusted by running alsamixer on the terminal, Pressing F6 to choose the soundcard then F5 to show all channels (in and out).

### 6.3.1 GRBL and Octoprint

The Arduino nano is running GRBL, a 3d printing firmware. In order to achieve ease of use and the best precision possible, this firmware has been proven far superior to custom-made solutions. The pinout of the arduino nano is as follows :


Figure 6.5: Arduino nano GRBL pinout

The firmware belives the left wheel is the X axis and the right wheel is the Y axis and thus pins : D8,D6,D5,D2,D3 are connected to the corresponding pins on each of the stepper drivers. The following picture illustrates the pinout for each stepper driver :


Figure 6.6: DRV8825 stepper driver pinout[6]

The raspberry pi pinout is as follows :

Figure 6.7: Raspberry Pi pinout[5]

The important pins to keep in mind :

- I2c GPIOs : used for communication with the laser sensors.
- GPIOs 26 and 21 : connected to the XSHUNT pins of laser sensors left and right respectively.
- GPIO 20 : used for servo motor PWM signal generation.
- GPIO 16 : used for external relay control.

The arduino Nano is connected to the raspberry pi via USB. Once the SSH connection established the user enters the following command in the terminal

/OctoPrint/venv/bin/octoprint serve

The command starts the Octoprint webserver and it can now be accessed from any computer or phone at the following address : https://*RaspberryPILocalAddress*:5000
Now that the server is started, one needs to configure some parameters relative to the robot :
By opening the the Octoprint webpage we see :


Figure 6.8: Octoprint web interface

- In Yellow : the general state of the robot, Print corresponds to starting the movement. Pause and Cancel buttons work as intended
- In Blue : the communication terminal. Allows to set some important parameters
- In Red : the uploaded gcode files ( corresponds to the trajectories )
- In Purple : the button to command the electrical relay for the experimentation setup layer

Before controlling the robot, some important general parameters need to be set. By sending $$ to the microcontroller through the communication terminal, the value of global variables is displayed (max speed, acceleration, steps per mm). To change a parameter, one needs to send $*ID*=*VALUE*, with *ID* being the parameter’s ID and *VALUE* the desired value. From the full list of parameters[2]
, one needs to know :

- *ID*=1 corresponds to the delay in milliseconds after a movement before the motors are turned off. Setting this value to 255 ensures the motors are always on (highest precision)
- *ID*=100 and *ID*=101 correspond to the number of steps per mm for the X axis and Y axis respectively. Refer to the inverse kinematic to compute this parameter. This value can be calibrated by commanding a set distance and observing the travelled distance. The new number of steps s’ can be computed with the following formula : s

0 = s ∗ (δx + 1) with s being the old number of steps per mm and δx the relative error on the travelled distance.

- *ID*=110 and *ID*=111 correspond to the max speed in mm/min for the X axis and Y axis (right and left wheels)
- *ID*=120 and *ID*=121 correspond to the acceleration rate in mm/s²
for the X axis and Y axis (right and left wheels)

In order to move the robot, Gcode needs to be executed. Gcode is a simple text file containing successive movement commands interpreted by the micro controller. Two main commands to know :

- G91 X*DIST1* Y*DIST2* commands the right wheel to relatively move by *DIST1* [mm] and left wheel to move by *DIST2* [mm]. Refer to the inverse kinematics to understand what distances are needed for what type of motion
- G92 X0 Y0 resets the internal coordinates in terms of travelled X and Y distances. This command is only necessary if one uses G90 which is absolute positioning and not G91 relative positioning

Once the gcode file ready and saved as for instance "trajectory.gcode", one can simply drag and drop the file to the Octoprint interface and press print to start the trajectory following.

- For the indoor wifi localization experiment, do not forget to turn on the RTT with the corresponding switch 6.3.1
- For the echoSLAM experiment, the Gcode file is slightly modified to include a custom command. Upon inter-preting the custom command, the microcontroller stops the motors and the raspberry pi runs the experiment before allowing the microcontroller to resume the trajectory following.

A script to generate g-code files from x,y cartesian coordinates is provided. The script differentiates between both experiments and adds or not the custom instruction for the echoSLAM experiment.

### 6.3.2 Custom scripts

With Octoprint being the new interface, only one script is needed : "gcode.py". This script parses and translates a text file into gcode. The text file is a succession of lines with the following format i,angle,dist,x,y. With i the index of the point (or measurement) , angle the angle of in position rotation, dist the distance to travel,x the distance to be travelled by the left wheel, y the distance to be travelled by the left wheel.

- For the indoor wifi localization experiment, simply put 0 on the angle and dist values and input the x and y distances travelled by both wheels directly.
- For the echoSLAM experiment, simply ignore the last two elements of the formatted line

To run the script simply call python3 gcode.py *EXP_ID* *NUM_ORIEN* *MIN_FREQ* *MAX_FREQ* *DURATION*

- *EXP_ID* being the expermentation ID , 0 for the EchoSlam ,1 for the indoor wifi localization
- *NUM_ORIEN*,*MIN_FREQ*,*MAX_FREQ*,*DURATION* concerns only the EchoSlam correspond respectively to the number of orientations of the speaker on each sound experiment, the minimum frequency of the sweep, the max frequency of the sweep and duration of the sweep.
- Ignore all arguments that do not concern the current experiment.

# 7 | Bibliography

[1] RS | Components. | Stepper | motors | and | drives, | what | is | full | step, | half
step | and | microstepping? | https://www.rs-online.com/designspark/
stepper-motors-and-drives-what-is-full-step-half-step-and-microstepping, (https://www.rs-online.com/designspark/stepper-motors-and-drives-what-is-full-step-half-step-and-microstepping) | Consulted | on | the
7th June 2019.
[2] GNEA. Grbl v1.1 configuration. https://github.com/gnea/grbl/wiki/Grbl-v1.1-Configuration, Consulted on the 7th June 2019.
[3] Hackaday. | How | accurate | is | microstepping | really? | https://hackaday.com/2016/08/29/
how-accurate-is-microstepping-really/, (https://hackaday.com/2016/08/29/how-accurate-is-microstepping-really/) Consulted on the 7th June 2019.
[4] Robot Platform. Wheel control theory. http://www.robotplatform.com/knowledge/Classification_of_Robots/wheel_control_theory.html, (http://www.robotplatform.com/knowledge/Classification_of_Robots/wheel_control_theory.html) Consulted on the 7th June 2019.
[5] Polulu. Drv8825 stepper motor driver carrier, high current. https://www.pololu.com/product/2133, Consulted on the 7th June 2019.
[6] Raspberry Spy. Simple guide to the raspberry pi gpio header. https://www.raspberrypi-spy.co.uk/2012/06/simple-guide-to-the-rpi-gpio-header-and-pins/, (https://www.raspberrypi-spy.co.uk/2012/06/simple-guide-to-the-rpi-gpio-header-and-pins/) Consulted on the 7th June 2019.
